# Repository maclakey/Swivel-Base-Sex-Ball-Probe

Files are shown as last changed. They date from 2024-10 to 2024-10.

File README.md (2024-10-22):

# Swivel-Base-Sex-Ball-Probe
Sex ball probe for calibrating offsets between toolheads

This is a ball probe meant to be used with https://github.com/viesturz/NozzleAlign<br><br>
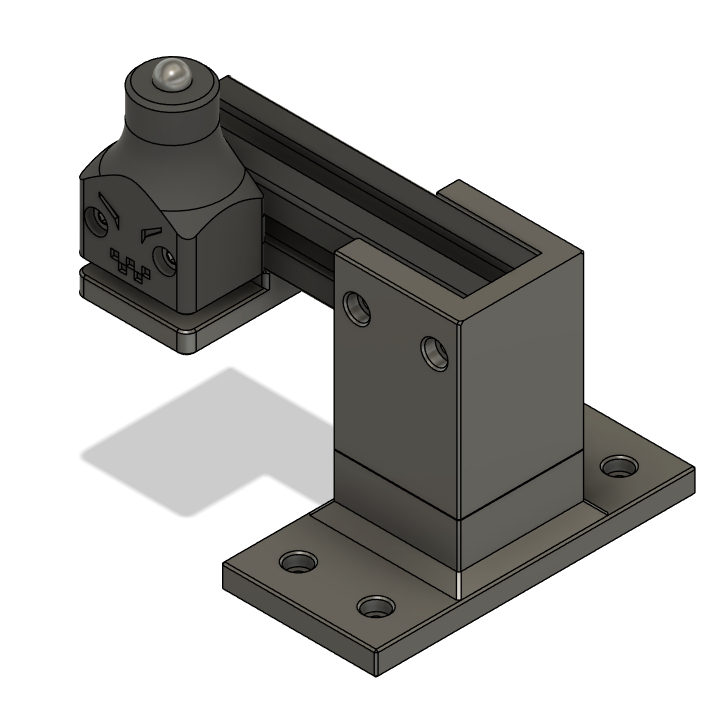
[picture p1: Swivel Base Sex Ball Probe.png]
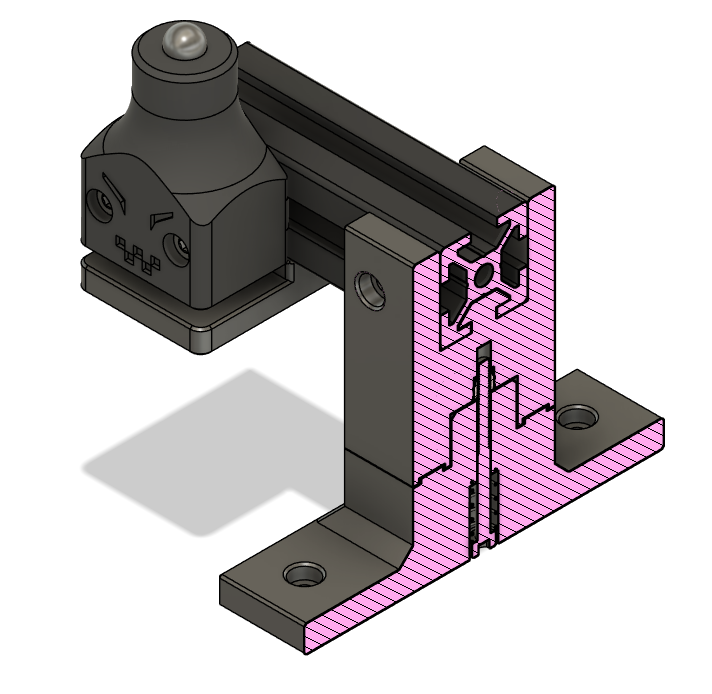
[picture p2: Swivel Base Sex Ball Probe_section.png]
 

**BOM:** <br>
1 - 7mm steel ball<br>
1 - 30mmx5mm steel shaft<br>
1 - m3x35 SHCS<br>
2 - m3x20 SHCS<br>
1 - m3 Brass threaded insert<br>
1 - 12x6mm spring<br>
1 - 80mm length of 2020 aluminum extrusion<br>
1 - Omron 2DF-F microswitch<br>
1 - JST 2 (or 3) pin receptical<br>
some m3x8 screws.  no more than 8 <br>
some m3 roll-in nuts, no more than 10<br>
some m3 hammer head nuts<br>
<br>
**Instructions:** <br>
<br>
**Printing the parts:**<br>
Print the parts using ABS with the standard Voron print settings.<br>
The .3mf file contains all the parts at their preferred printing orientations.  <br>
You should not need supports.<br>
<br>
**Swivel base:**<br>
Assemble as shown in the CAD file.  <br>
Carefully insert the heat-set brass threaded insert into the center of the Base Top.  <br>
The spring goes on the M3x35 SHCS which then goes up through the Base Flange and screws into the brass insert in the base top.<br>
Tighten the screw until it holds the pieces together firmly.  You should, with a little effort, be able to swivel the top which will lock into place on the alignment grooves.<br>
Slide the extrusion into the base top.  It's a snug fit, but if you want it even more secure, you can fasten it with four m3x8 screws and 4 m3 roll-in nuts.<br>
<br>
**Nozzle Probe:**<br>
Screw the microswitch into it's place, making sure the button is visible in the hole.<br>
Solder some lengths of wire between the microswitch and the JST receptical.<br>
Fasten the nozzle probe to the free end of the 80mm extrusion using two m3x20 and either m3 roll-in or hammer-head nuts.<br>
<br>
**Attach to printer:**<br>
This is designed to attach to the front of the printer, assuming you have the extra frame attached for holding the docks in for TAP Changer. ( https://github.com/viesturz/tapchanger?tab=readme-ov-file )<br>
using 4 - m3x8 screws and 4 roll-in nuts, fasten the base down to the frame so that the arm hangs over the bed.<br>
now gently drop in the 30mm shaft followed by placing the ball on top.<br>
<br>
You can now swivel the arm out of the way when not in use, and back again when/if you need to calibrate the tool offsets again.<br>
This should keep you from having to re-calibrate the nozzle probe location. <br>

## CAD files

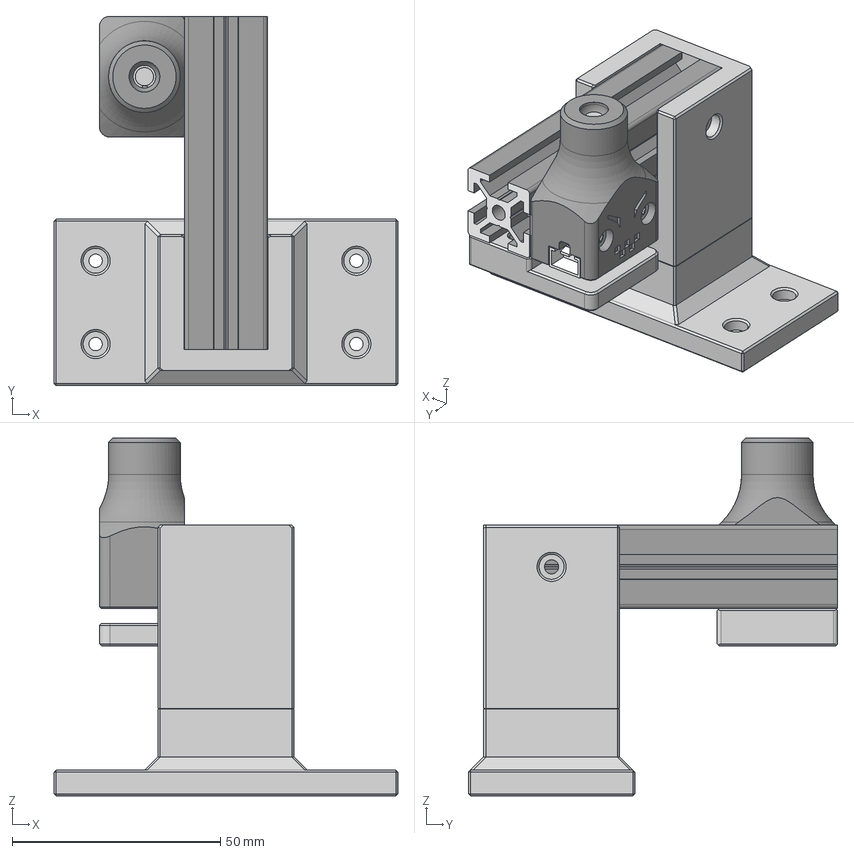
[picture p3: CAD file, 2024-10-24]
Swivel Base Sex Ball Probe.step
82.6 x 88.7 x 85.9 mm
Omron_D2F_F
5x30 Shaft
JST 3pin Recepticle
M3x20 SHCS (19)
M3x20 SHCS (18)
M3 Threaded Insert (57)

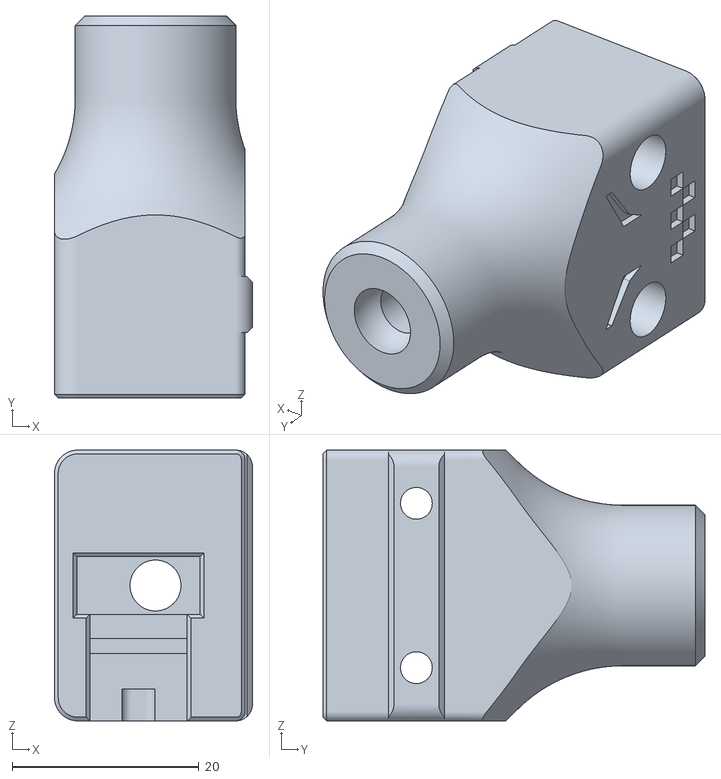
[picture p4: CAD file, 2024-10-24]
Swivel nozzle_probe.stl
21.2 x 40.9 x 29.0

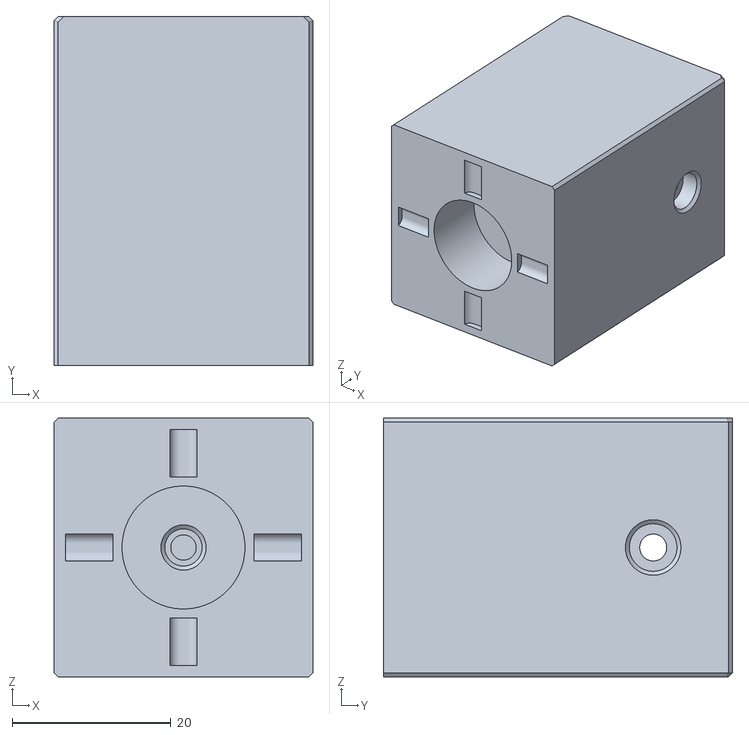
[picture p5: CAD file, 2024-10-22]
Swivel Base top.stl
32.6 x 44.0 x 32.6

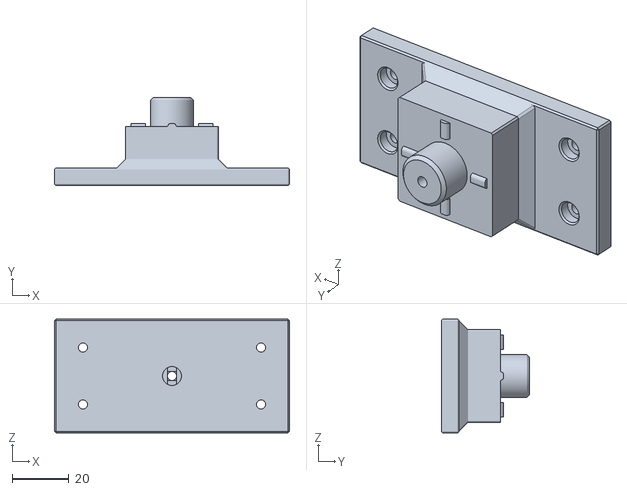
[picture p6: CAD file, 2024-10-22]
Swivel Base flange.stl
82.6 x 31.0 x 40.0

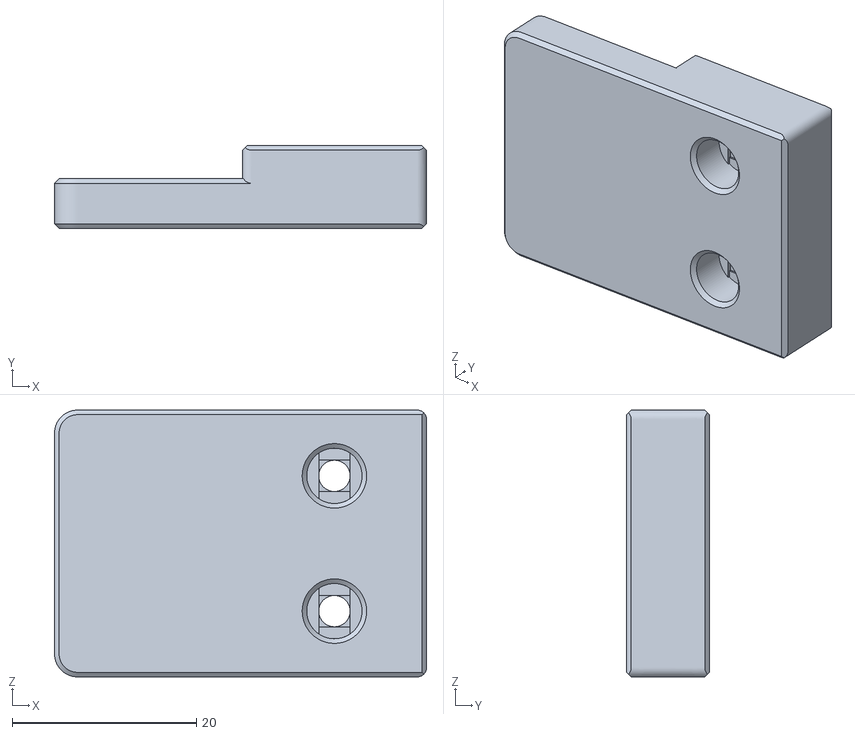
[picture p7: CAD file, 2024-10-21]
Swivel Bed Spacer.stl
40.4 x 9.00 x 29.0

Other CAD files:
Swivel Base sex ball probe.3mf

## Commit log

2024-10-21 added images and .step file
    [Swivel Base Sex Ball Probe v4.step]
2024-10-21 Update Swivel Base top.stl
    [Swivel Base top.stl]
2024-10-21 Create Swivel Base Sex Ball Probe v5.step
    [Swivel Base Sex Ball Probe v5.step]
2024-10-22 Update Swivel Base Sex Ball Probe.png
2024-10-22 updated spring cavity
    [Swivel Base flange.stl, Swivel Base sex ball probe.3mf]
2024-10-22 updated base top and step file
    [Swivel Base Sex Ball Probe v4.step, Swivel Base Sex Ball Probe v5.step, Swivel Base Sex Ball Probe.step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]
2024-10-24 Update Swivel nozzle_probe.stl
    [Swivel nozzle_probe.stl]
2024-10-24 updated height of chimney to accommodate a stack of magnets instead of a shaft
    [Swivel Base Sex Ball Probe.step]
